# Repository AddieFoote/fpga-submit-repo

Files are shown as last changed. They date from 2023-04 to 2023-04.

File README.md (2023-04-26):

# Running the Code in Simulation

## Verilog
### Simulate PWM
run `make pwm` then `make run` in simulation_files directory then open the vcd file in GTKwave

### Simulate entire control
1. uncomment import statements and vcd dump statements from verilog code in simulation_files and real_robot
2. from the simulation_files directory, run `make driver` then `make run` in simulation_files directory
3. open the vcd file in GTKwave
4. if desired, change the inputs in the run_drive.v file, also can change them based on the clock to see dynamic change
5. additionally, change the mode in drive.v
6. to change which files variables are dumped, comment out/uncomment the dump commands from the verilgo files in simulation_files and real_robot

## Control/Image Processing Files
For the image processing files, they're written in python, so you can just run it with `python <name of file>`. However, the pyparticle files and methods written to pass information to the IOT device must be commented out to run just the python code. To test the image processing on a video other than the default webcam, change the line `cap = cv2.VideoCapture(0)` to `cap=cv2.VideoCapture(<path to video in directory>)` so for example, I've included a video rgb_person.mp4 in the same directory so you could use `cap=cv2.VideoCapture('rgb_person.mp4)`
The same goes for the controller python file, lines `robot.writeMotor(write_string)` and any other lines with `robot.writeMotor`, `robot.led`, or any addtional pyparticle functions using the `robot` object must be commented out. I've included comments telling you exactly which lines.
 
# Running on Hardware
## Mechanical Stuff
1. 3D print two of the stl files in STL_files, wheel.stl and servo_mount.stl
2. Attach the hubs provided with the servos to wheels the with the provided screws
3. Cut a 12x12 piece of quarter inch plywood
4. Use wood screws to secure the 3D printed servo attachment in the corner with the square hole facing outwards 
5. use 8 1 inch 8-32 bolts and lock nuts to secure the servos to the attachment
6. attach wheels to servo: pressfit with the hubs and servos and add the provided bolt
7. Attach 2 small castor-type wheels to the front 
8. Secure the fpga board and electronics to the open space

## Electrical configuration
1. Connect the fpga to 12 V DC power
2. Power the particle photon board by connecting the 5 volt pin on the fpga to the VIN pin on the particle photon (on the fpga 6th down on the left side when the red button is oriented at the top left, on the photon the pin is labeled). Also connect ground to ground (right of 5V on fpga, labeled on photon)
3. Connect pins A0, A1, A2, A3, A4, A5 on the particle board to to 15, 17, 19, 21, 25 on the FPGA respectively. Also connect D0, D1, D2, D3, D4, D5 to 14, 16, 18, 20, 22.
4. Connect servos to 4.8-7 V power supply (red wire power, brown wire ground)
5. Connect GPIO pin 5 and 7 on the FPGA to left servo and right servo control signal (the orange wire) respectively

## Particle Photon Board Setup
1. download the mobile app
2. run `Pip install pyparticleio`
3. Create a particle account 
4. Create an access token
5. Create a file for the access token: image_prc/secret.py and write 1 line `access_token = "put your access token here"`
6. run `particle compile photon .`
7. Plug photon into computer and press the button 
8. Run `particle flash FPGA_Robot photon_firmware_1682006758610.bin` substituting FPGA_Robot with the name given to your project and photon_firmware_1682006758610.bin with the result of compiling the .ino file 

## FPGA setup
1. Install Quartus (Quartus Prime 22.1std)
2. Install the hardware driver for the usb blaster
   * On the off chance your computer has security restrictions like ours you may be able to download it on a different device, unzip it, change all the .dll files to .txt, rezip it, upload to one drive, download, unzip, change it back, rezip, and install
3. Open Quartus and click open project, select drive .qpf 
4. Double click compile design
5. Double click program device 
6. Select hardware setup and select USB blaster
7. Click auto detect
8. Click start

## Putting it all together
1. Now the functions in the c++ code are on the photon so you can call them from python given you are connected, download other dependencies. For the GUI and vision 
2. `Pip install PyQt5`
3. `Pip install numpy`
4. `Pip install opencv-python`
5. Either run the controller or image file and use the GUI
   1. `python controller.py`
   2. `python colorblob.py`

NOTE: to switch between controller mode and image blob mode requires actual changes to the verilog. Change line 12 in drive.v to 1’b0 if it’s control mode and 1’b1 for image. To run, recompile and run it. The reason for this is because we intend to set a GPIO port on the Particle board and read it from the FPGA to control the mode so it is automatic, however the FPGA broke before we got to it, so we haven’t made this simple change yet.

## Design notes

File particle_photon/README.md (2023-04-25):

# particle_photon

A Particle project named particle_photon

## Welcome to your project!

Every new Particle project is composed of 3 important elements that you'll see have been created in your project directory for particle_photon.

#### ```/src``` folder:  
This is the source folder that contains the firmware files for your project. It should *not* be renamed. 
Anything that is in this folder when you compile your project will be sent to our compile service and compiled into a firmware binary for the Particle device that you have targeted.

If your application contains multiple files, they should all be included in the `src` folder. If your firmware depends on Particle libraries, those dependencies are specified in the `project.properties` file referenced below.

#### ```.ino``` file:
This file is the firmware that will run as the primary application on your Particle device. It contains a `setup()` and `loop()` function, and can be written in Wiring or C/C++. For more information about using the Particle firmware API to create firmware for your Particle device, refer to the [Firmware Reference](https://docs.particle.io/reference/firmware/) section of the Particle documentation.

#### ```project.properties``` file:  
This is the file that specifies the name and version number of the libraries that your project depends on. Dependencies are added automatically to your `project.properties` file when you add a library to a project using the `particle library add` command in the CLI or add a library in the Desktop IDE.

## Adding additional files to your project

#### Projects with multiple sources
If you would like add additional files to your application, they should be added to the `/src` folder. All files in the `/src` folder will be sent to the Particle Cloud to produce a compiled binary.

#### Projects with external libraries
If your project includes a library that has not been registered in the Particle libraries system, you should create a new folder named `/lib/<libraryname>/src` under `/<project dir>` and add the `.h`, `.cpp` & `library.properties` files for your library there. Read the [Firmware Libraries guide](https://docs.particle.io/guide/tools-and-features/libraries/) for more details on how to develop libraries. Note that all contents of the `/lib` folder and subfolders will also be sent to the Cloud for compilation.

## Compiling your project

When you're ready to compile your project, make sure you have the correct Particle device target selected and run `particle compile <platform>` in the CLI or click the Compile button in the Desktop IDE. The following files in your project folder will be sent to the compile service:

- Everything in the `/src` folder, including your `.ino` application file
- The `project.properties` file for your project
- Any libraries stored under `lib/<libraryname>/src`

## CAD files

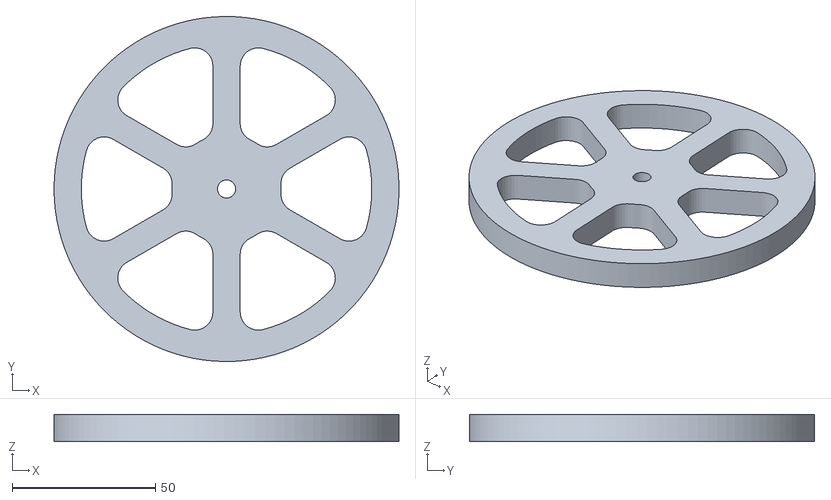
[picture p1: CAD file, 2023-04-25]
STL_Files/wheel.stl
120.4 x 120.4 x 9.52

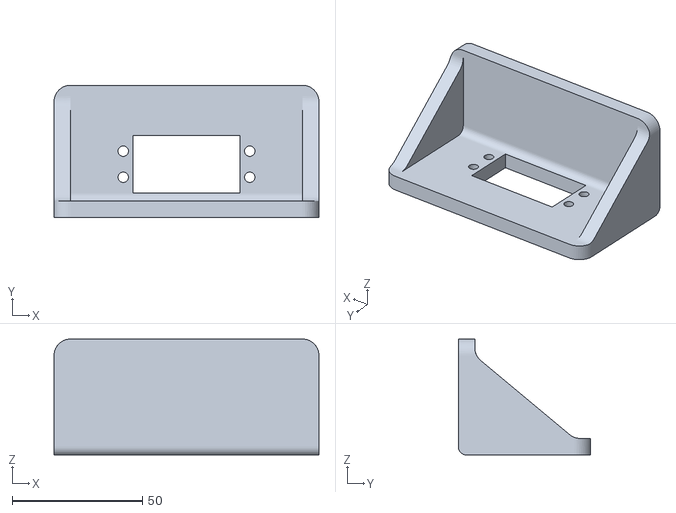
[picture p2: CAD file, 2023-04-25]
STL_Files/servo_mount.stl
101.6 x 50.8 x 44.5

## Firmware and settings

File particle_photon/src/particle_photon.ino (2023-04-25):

// copy paste pins
const pin_t _WKP = WKP;
// const pin_t _DAC = A6;
const pin_t _A5 = A5;
const pin_t _A4 = A4;
const pin_t _A3 = A3;
const pin_t _A2 = A2;
const pin_t _A1 = A1;
const pin_t _A0 = A0;
const pin_t _D7 = D7;
const pin_t _D6 = D6;
const pin_t _D5 = D5;
const pin_t _D4 = D4;
const pin_t _D3 = D3;
const pin_t _D2 = D2;
const pin_t _D1 = D1;
const pin_t _D0 = D0;
int analogvalue;

// allows code to run before the cloud is connected.
SYSTEM_THREAD(ENABLED);

// This function is called when the Particle.function is called
int ledToggle(String command)
{
    if (command.equals("on"))
    {
        digitalWrite(_D7, HIGH);
        return 1;
    }
    else if (command.equals("off"))
    {
        digitalWrite(_D7, LOW);
        return 0;
    }
    else
    {
    // Unknown option
    return -1;
    }
}

int writeBitStream(String bits) {
    //write motor value bit by bit
    digitalWrite(_A5, bits.charAt(0) == '1');
    digitalWrite(_A4, bits.charAt(1) == '1');
    digitalWrite(_A3, bits.charAt(2) == '1');
    digitalWrite(_A2, bits.charAt(3) == '1');
    digitalWrite(_A1, bits.charAt(4) == '1');
    digitalWrite(_A0, bits.charAt(5) == '1');

    digitalWrite(_D5, bits.charAt(6) == '1');
    digitalWrite(_D4, bits.charAt(7) == '1');
    digitalWrite(_D3, bits.charAt(8) == '1');
    digitalWrite(_D2, bits.charAt(9) == '1');
    digitalWrite(_D1, bits.charAt(10) == '1');
    digitalWrite(_D0, bits.charAt(11) == '1');
    return 0;
}

int setMode(String mode) {
    if (mode.equals("color"))
    {
        digitalWrite(_D7, HIGH);
        return 1;
    }
    else if (mode.equals("joystick"))
    {
        digitalWrite(_D6, LOW);
        return 0;
    }
}

// The setup() method is called once when the device boots.
void setup()
{  
    //define pinmodes
    pinMode(_WKP, OUTPUT);
    pinMode(_A5, OUTPUT);
    pinMode(_A4, OUTPUT);
    pinMode(_A3, OUTPUT);
    pinMode(_A2, OUTPUT);
    pinMode(_A1, OUTPUT);
    pinMode(_A0, OUTPUT);

    pinMode(_D7, OUTPUT);
    pinMode(_D6, OUTPUT);
    pinMode(_D5, OUTPUT);
    pinMode(_D4, OUTPUT);
    pinMode(_D3, OUTPUT);
    pinMode(_D2, OUTPUT);
    pinMode(_D1, OUTPUT);
    pinMode(_D0, OUTPUT);

    //define functions
    Particle.function("writeMotor", writeBitStream);
    Particle.function("led", ledToggle);
    Particle.function("mode", setMode);
    Particle.variable("analogvalue", analogvalue);
}

void loop()
{
}
